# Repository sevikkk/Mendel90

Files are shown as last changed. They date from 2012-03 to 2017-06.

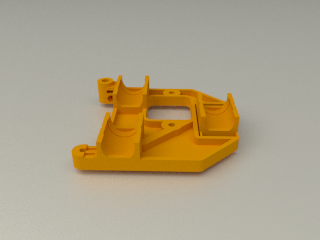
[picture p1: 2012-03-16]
sturdy/render/x_carriage.png

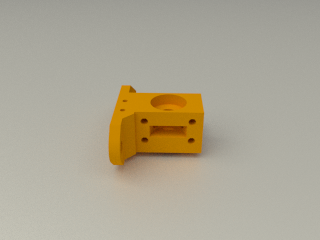
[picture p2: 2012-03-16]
sturdy/render/wades_block.png

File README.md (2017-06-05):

Standard variants
-----------------
[dibond](https://github.com/nophead/Mendel90/tree/master/dibond) is the version that was sold as a kit with 3mm sheets, 8mm rods and uses nuts and machine screws through the frame.

[sturdy](https://github.com/nophead/Mendel90/tree/master/sturdy) is 12mm MDF sheets, 10mm rods and uses wood screws into pilot holes in the frame. It can be built without CNC.

[mendel](https://github.com/nophead/Mendel90/tree/master/mendel) is 6mm acrylic sheets with a 10mm acrylic base, 8mm rods and uses machine screws into tapped holes in the frame.

[huxley](https://github.com/nophead/Mendel90/tree/master/huxley) is a scaled down version of dibond using 6mm rods and NEMA14 motors.

The dibond, sturdy and mendel versions can be modified to accept the E3D v6 hot end. The files that change are [dibond_E3D](https://github.com/nophead/Mendel90/tree/master/dibond_E3D)
and [sturdy_E3D](https://github.com/nophead/Mendel90/tree/master/sturdy_E3D).

Limitations
-----------
The dibond and sturdy versions are well tested and popular. The acrylic version, called mendel, hasn't been built for a long time and is not recommened.
The Huxley version hasn't been tested in its final form although one prototype has been made of an earlier version and a few snags fixed since.

Use
---
Add the directory of the OpenScad executable to your search path. OpenSCAD-2015.05 or later is required.
To get PDF versions of the sheet drawings add InkScape to your search path.

To make all the files for a machine run
```python
make_machine.py machine_name
```

To make just the bom, sheets or stls run bom.py, sheets.py or stls.py machine\_name.

machine\_name can be dibond, mendel, sturdy or huxley. To make your own variant copy scad\conf\mendel\_config.scad or scad\conf\sturdy\_config.scad to yourname\_config.scad.  Then run `make_machine.py yourname`.

To view the model of the whole machine, open scad\main.scad. It will take several minutes to render (about about 5 minutes on my computer) but after that you can pan and zoom it at reasonable speed and changes takes less time to render.  (Note: main.scad will only render correctly if conf\machine.scad exists, which is created by the make_machine.py script.)

To view a sub-assembly, open the individual scad files. Set the exploded flag in config.scad to make exploded views.

To get blender renders of all the parts put blender in your search path and run `render.py machine_name`.

Credits
-------
Fan model based on [this model](http://www.thingiverse.com/thing:8063) by MiseryBot, CC license.

[Sanguinololu model](http://www.thingiverse.com/thing:18606) by ax\_the\_b, CC license.

Spring taken from openscad example 20

x-end.scad and wade.scad use some elements of the Prusa ones by Josef Prusa, GPL license.

z_couplings originally based on [this model](http://www.thingiverse.com/thing:7153) by Griffin_Nicoll, GPL license.

Bearing holders originally based on [this model](http://www.thingiverse.com/thing:7755) by Jolijar, CC license.

InkCL.py based on [this code](http://kaioa.com/node/42)

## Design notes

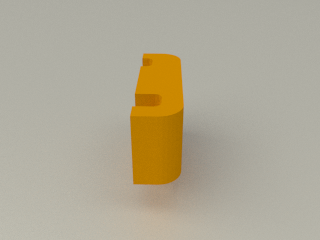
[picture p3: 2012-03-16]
sturdy/render/cable_clip_AB.png

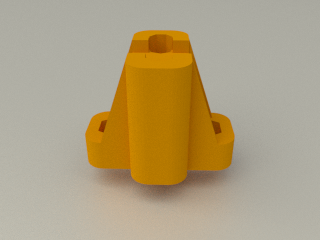
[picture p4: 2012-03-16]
sturdy/render/y_belt_anchor.png

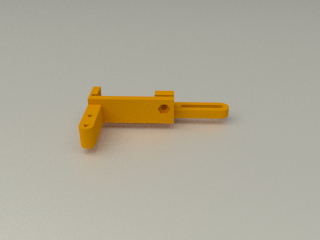
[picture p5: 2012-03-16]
sturdy/render/z_limit_switch_bracket.png

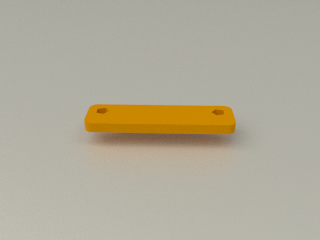
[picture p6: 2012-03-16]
sturdy/render/d_shell_lid.png

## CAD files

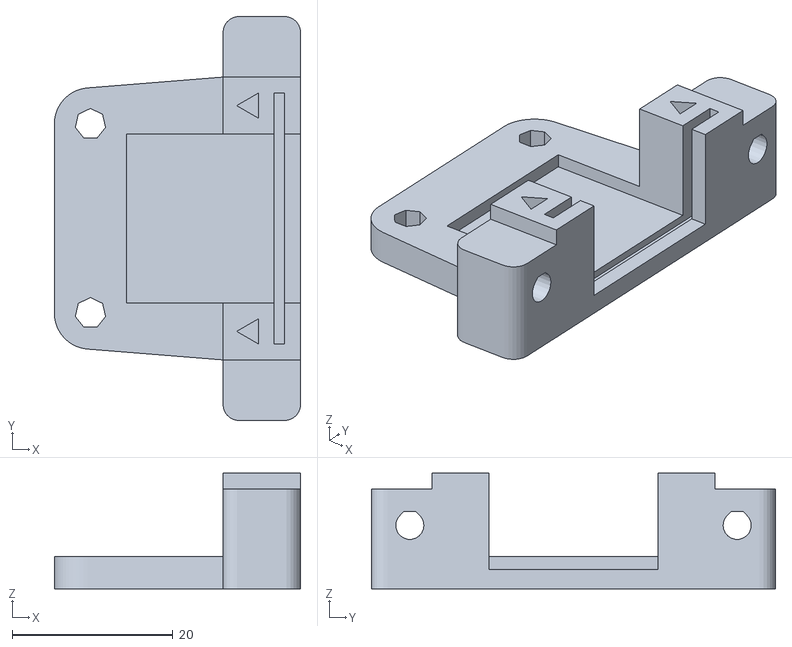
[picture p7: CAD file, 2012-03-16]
mendel/stls/d_shell.stl
30.7 x 50.3 x 14.4

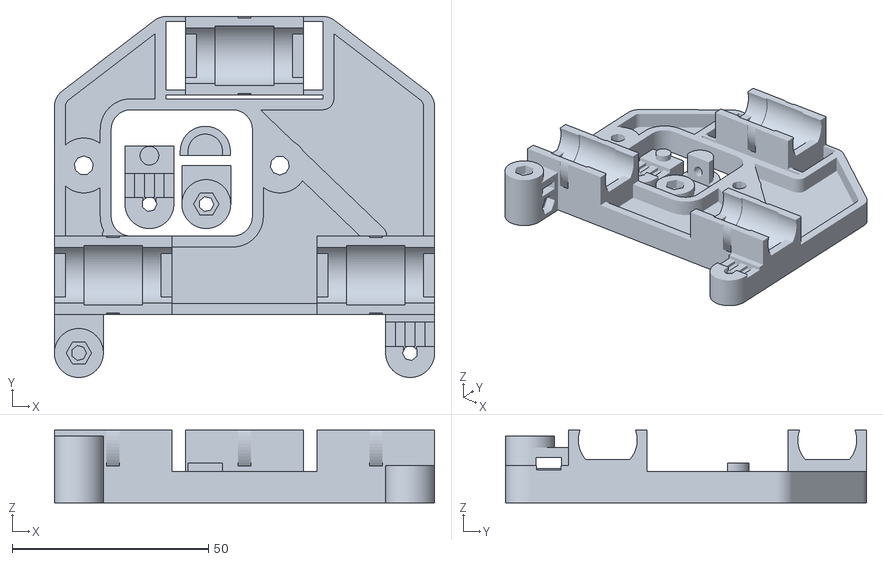
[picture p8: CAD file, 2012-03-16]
mendel/stls/printed/x_carriage_parts.stl
97.0 x 92.1 x 18.5

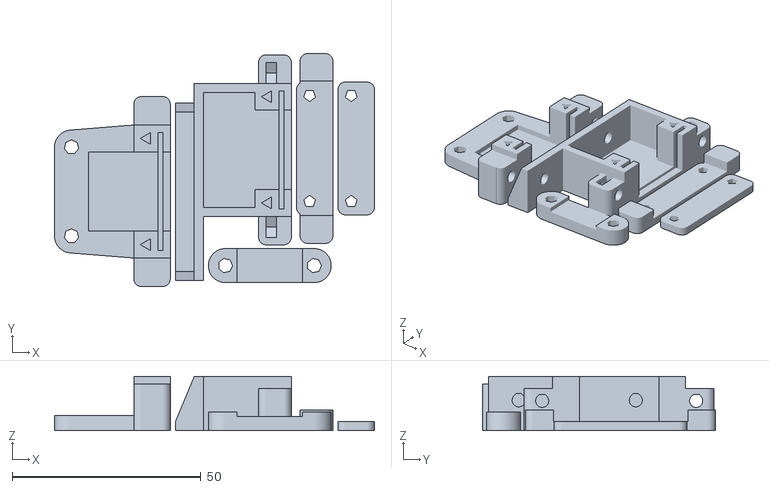
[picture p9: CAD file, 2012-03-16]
sturdy/stls/printed/d_motor_brackets.stl
84.7 x 61.7 x 14.4

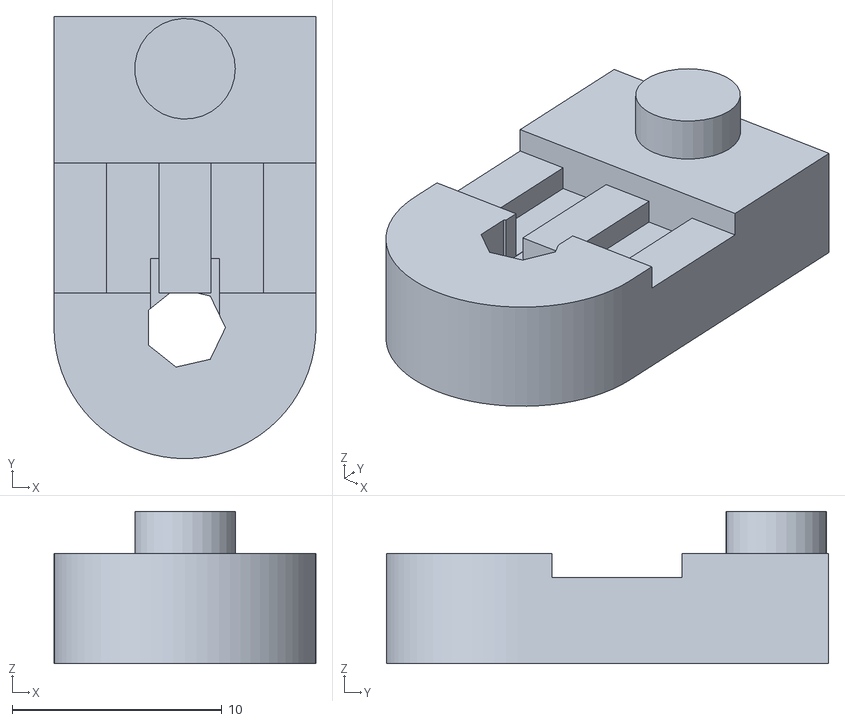
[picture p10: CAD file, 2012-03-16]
sturdy/stls/x_belt_grip.stl
12.5 x 21.1 x 7.26

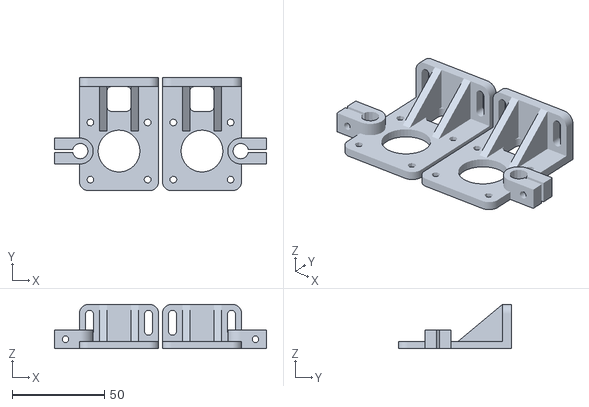
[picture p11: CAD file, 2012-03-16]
mendel/stls/printed/z_motor_brackets.stl
115.0 x 61.5 x 24.0

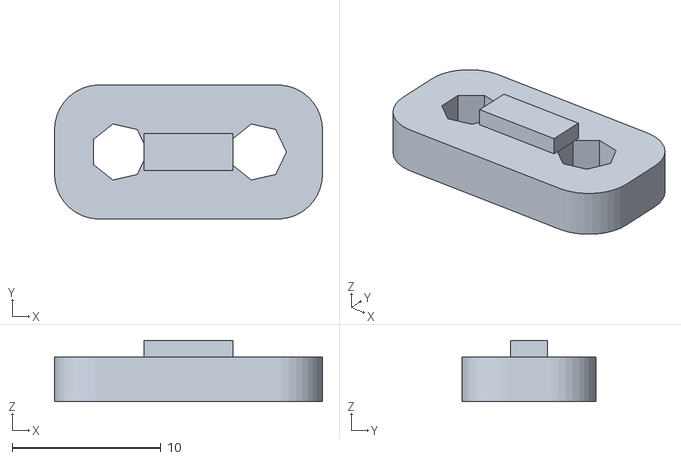
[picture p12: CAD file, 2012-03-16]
mendel/stls/y_belt_clip_toothed.stl
18.0 x 9.00 x 4.12

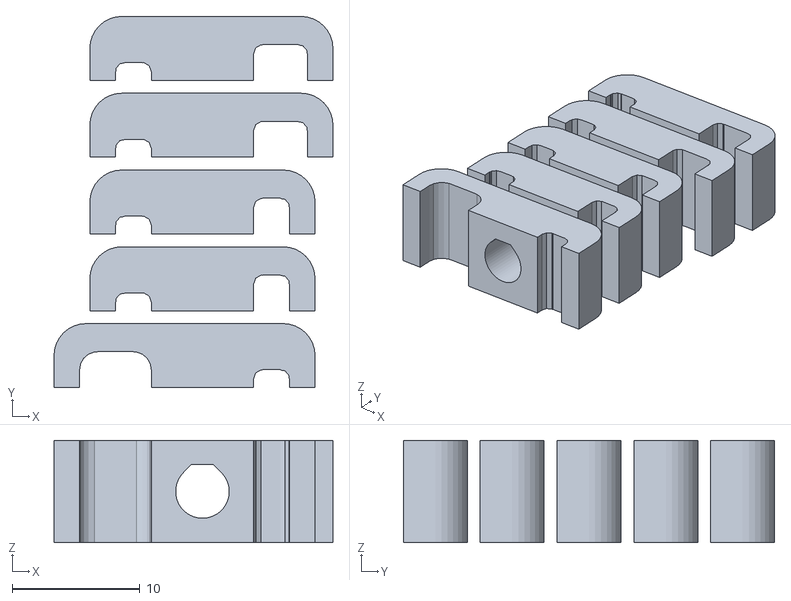
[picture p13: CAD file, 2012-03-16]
sturdy/stls/printed/cable_clips.stl
21.8 x 29.0 x 8.00

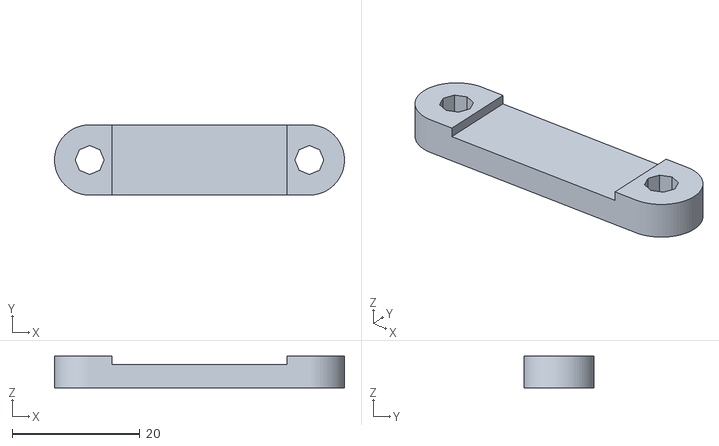
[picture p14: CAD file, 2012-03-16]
sturdy/stls/ribbon_clamp_20_40.stl
45.4 x 11.0 x 5.00

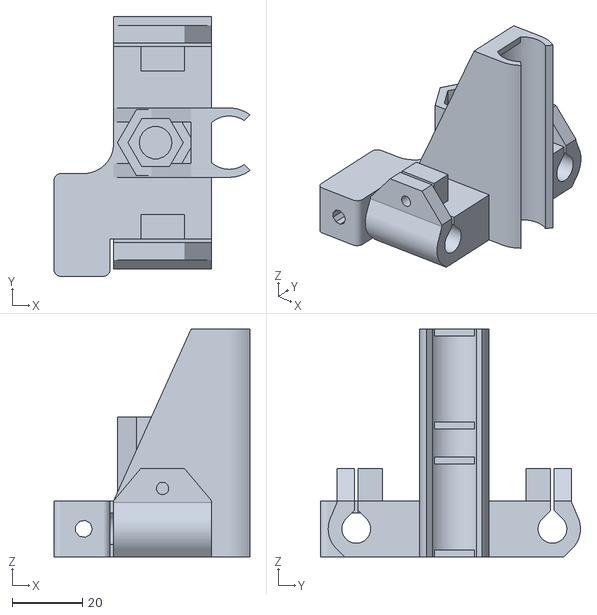
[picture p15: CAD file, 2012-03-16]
mendel/stls/printed/x_idler_bracket.stl
55.9 x 74.2 x 65.0

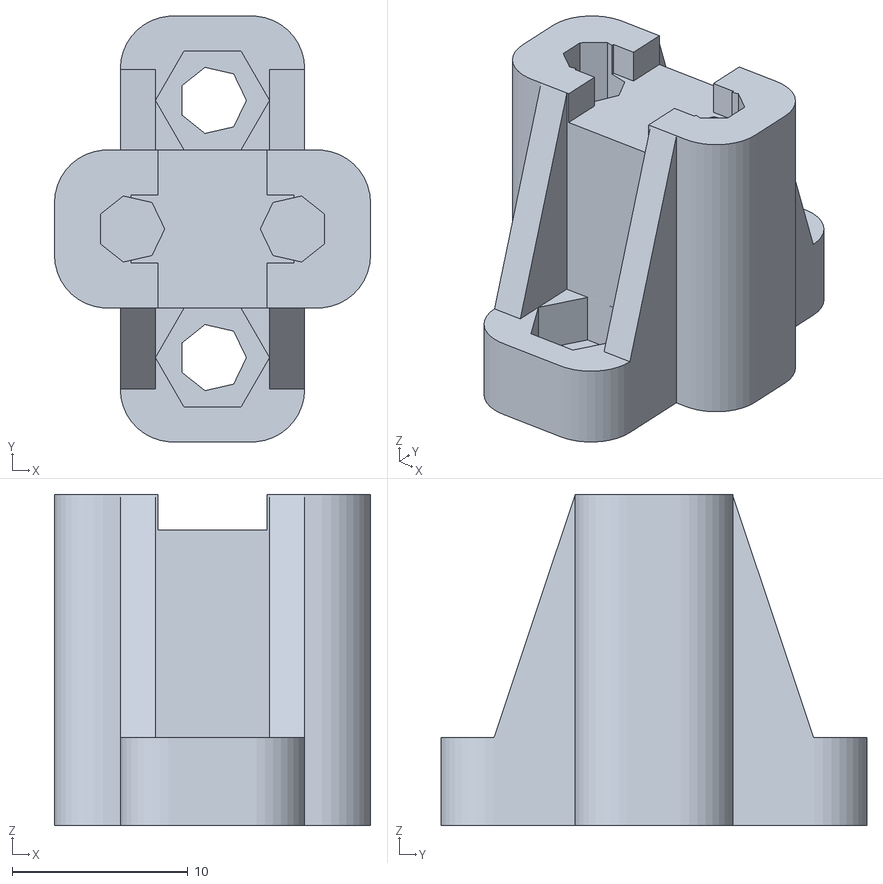
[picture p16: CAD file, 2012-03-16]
mendel/stls/y_belt_anchor.stl
18.0 x 24.3 x 18.9

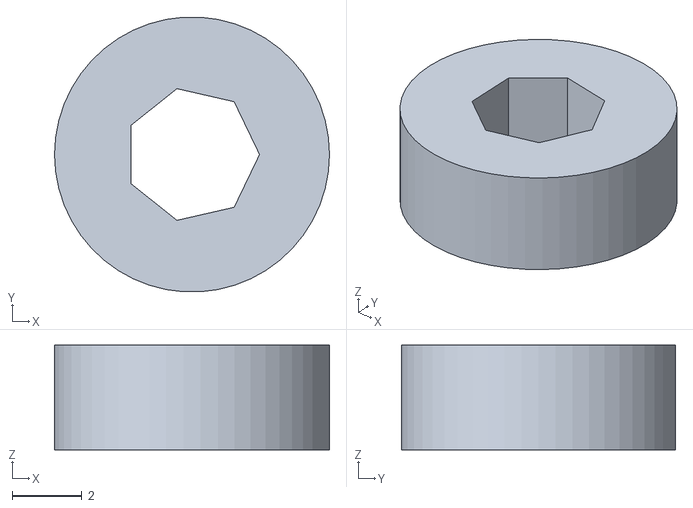
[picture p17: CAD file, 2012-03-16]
sturdy/stls/printed/pcb_spacer.stl
7.86 x 7.85 x 3.00

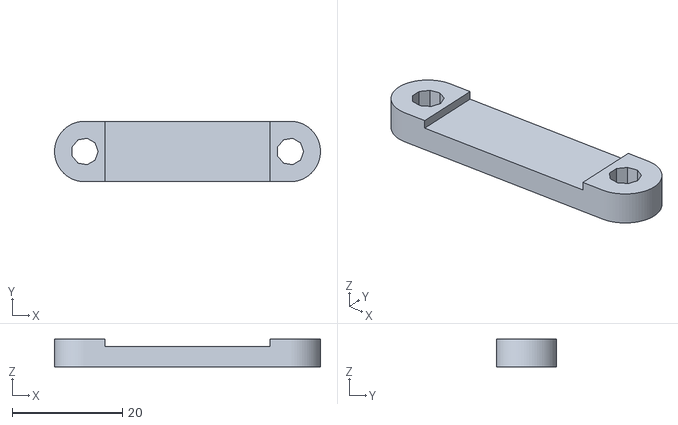
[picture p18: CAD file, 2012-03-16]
sturdy/stls/ribbon_clamp_22_44.stl
48.3 x 11.0 x 5.00

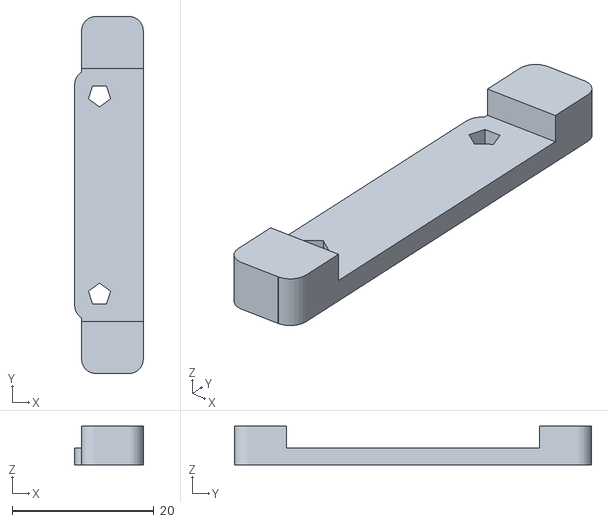
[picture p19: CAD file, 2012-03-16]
mendel/stls/d_motor_bracket_lid.stl
9.67 x 50.3 x 5.45

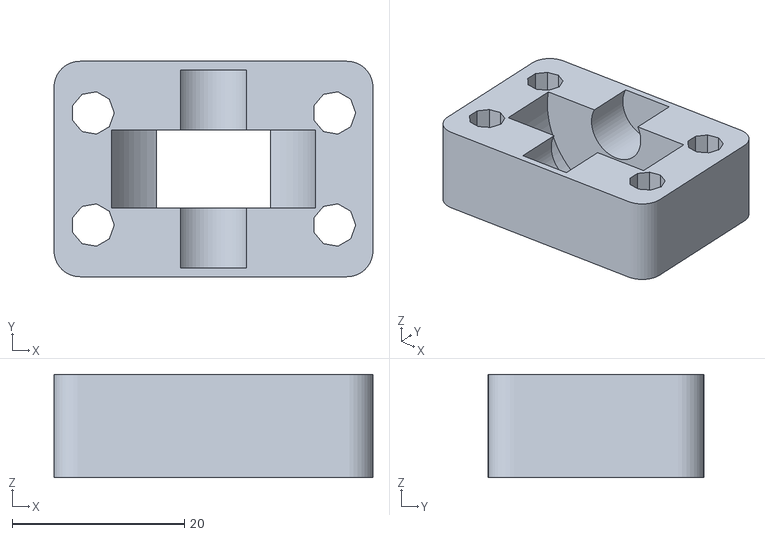
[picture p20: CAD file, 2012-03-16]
mendel/stls/printed/wades_idler_block.stl
37.0 x 25.0 x 12.0

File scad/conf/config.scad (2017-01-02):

//
// Mendel90
//
// GNU GPL v2
// nop.head@gmail.com
// hydraraptor.blogspot.com
//
// Configuration file
//
bom = $bom == undef ? 0: $bom;                 // 0 no bom, 1 assemblies and stls, 2 vitamins as well
exploded = $exploded == undef ? 0 : $exploded; // 1 for exploded view

show_jigs = true;               // show printed jigs required to build the machine
show_support = true;            // show support structures, must be set when generating STLs
show_rays = false;              // show light and camera rays to check orientation is correct

// Real-world colors for various parts & vitamins
use_realistic_colors = false;    // true for "real" colors, false for "distinct" colors (useful during design and for build instructions)
printed_plastic_color = "blue";
cable_strip_real_color = "fuchsia";
belt_real_color = "yellow";
bulldog_real_color ="black";

eta = 0.01;                     // small fudge factor to stop CSG barfing on coincident faces.
$fa = 5;
$fs = 0.5;

function sqr(x) = x * x;            // shortcut

module rotate(a)
{
 cx = cos(a[0]);
 cy = cos(a[1]);
 cz = cos(a[2]);
 sx = sin(a[0]);
 sy = sin(a[1]);
 sz = sin(a[2]);
 multmatrix([
  [ cy * cz, cz * sx * sy - cx * sz, cx * cz * sy + sx * sz, 0],
  [ cy * sz, cx * cz + sx * sy * sz,-cz * sx + cx * sy * sz, 0],
  [-sy,      cy * sx,                cx * cy,                0],
  [ 0,       0,                      0,                      1]
 ]) children();
}

cnc_tool_dia = 2.4;
layer_height = 0.4;
filament_width = layer_height * 1.5;
min_wall = 2 * filament_width + eta;
part_base_thickness = 5;;           // The thickness of things screwed to the frame

pcb_thickness = 1.6;
feed_tube_rad = 5 / 2;              // Filament feed tube
feed_tube_tape_rad = 6.2 / 2;
feed_tube_tape = 12;
function nozzle_length(hot_end) = max(54, hot_end_length(hot_end));    // how far nozzle extends below top of carriage

include <colors.scad>
include <utils.scad>
include <vitamins.scad>

endstop_wires    = [2, 1.4, "A"];   // 7 strands of 0.2
motor_wires      = [4, 1.4, "B"];
bed_wires        = [2, 2.8, "C"];   // 13A mains cable
fan_motor_wires  = [6, 1.4, "D"];   // fan and motor wires along top of gantry
two_motor_wires  = [8, 1.4,,"E"];   // Y and Z motors
thermistor_wires = endstop_wires;

endstop_wires_hole_radius = wire_hole_radius(endstop_wires);
motor_wires_hole_radius = wire_hole_radius(motor_wires);
two_motor_wires_hole_radius = wire_hole_radius(two_motor_wires);
fan_motor_wires_hole_radius = wire_hole_radius(fan_motor_wires);
bed_wires_hole_radius = wire_hole_radius(bed_wires);
thermistor_wires_hole_radius = wire_hole_radius(thermistor_wires);

cnc_sheets = false;                 // If sheets are cut by CNC we can use slots, etc instead of just round holes
base_nuts = false;                  // Need something under the base if using nuts
pulley_type = T5x8_plastic_pulley;
clip_handles = true;
include_fan = false;
squeeze = false;                    // Bodge to make Huxley as small as possible without affecting dibond kits
part_fan = fan60x15;
extruder = Wades;                   // Default extruder
raspberry_pi = false;               // Raspberry pi mounted on PSU
raspberry_pi_camera = false;        // RPI camera on bar across the back
light_strip = false;
vero_bed = false;                   // Bed made from vero board rather than custom PCB.
include <machine.scad>              // this file is generated from the command line parameter to include one of the machine configs

screw_clearance_radius = screw_clearance_radius(cap_screw);
nut = screw_nut(cap_screw);
nut_radius = nut_radius(nut);
nut_trap_depth = nut_trap_depth(nut);
washer = screw_washer(cap_screw);

bearing_clamp_tab = cnc_sheets ? (nut_radius(nut) + 3 * filament_width) * 2 : washer_diameter(washer) + 2;   // how much the lugs stick out and their width
bearing_clamp_tab_height = 4;           // thickness of the lugs

hole_edge_clearance = 5;                // how close a hole can be to the edge of a sheet
base_clearance = cnc_sheets ? 1 : 2;    // how close we get to the edge of the base
axis_end_clearance = cnc_sheets ? 1 : 2;// how close we get to the end of an axis
limit_switch_offset = 1;                // the over travel to reach the limit switch
X_carriage_clearance = 2;               // how close the X carriage is to the XZ plane
                                        // how close the Y carriage is to the window in the XZ plane
Y_carriage_clearance = 2 + (clip_handles ? (bulldog_handle_length(small_bulldog) - (Y_carriage_width - bed_width) / 2) : 0);
Y_carriage_rad = 3;                     // corner radius
Z_clearance = 10;                       // How close the top of the object gets to the gantry
belt_clearance = 0.2;                   // clearance of belt clamp slots

X_bar_dia = bearing_rod_dia(X_bearings);      // rod sizes to match the bearings
Y_bar_dia = bearing_rod_dia(Y_bearings);
Z_bar_dia = bearing_rod_dia(Z_bearings);

Y_idler_bearing = BB624;
X_idler_bearing = BB624;

extruder_ways = 4 + 6 + 2 + 1 + 1;      // motor + heater(x3) + thermistor + probe + fan = 14
x_end_ways = extruder_ways + 4 + 2;     // motor plus limit switch = 20
bed_ways = 24 + 2;                      // twelve each way for the current plus a thermistor

module wire_hole_or_slot(r) {
    if(cnc_sheets)
        rotate([0, 0, 90])
            slot(r = r, h = 100, l = 2 * r);
    else
        translate([0, r + hole_edge_clearance, 0])
            wire_hole(r);
}

function z_bar_offset() = round(NEMA_width(Z_motor)) / 2  + ((Z_bar_dia > 10) ? ((Z_bar_dia - 10) / 2) : 0);
echo("Z: ", z_bar_offset());

base_screw = sheet_is_soft(base) ? frame_soft_screw : (base_nuts ? frame_thin_screw : frame_thick_screw);
base_nut = base_nuts ? screw_nut(base_screw) : false;
base_nut_traps = base_nuts && cnc_sheets;
base_washer = screw_washer(base_screw);
base_screw_length = base_nuts ? screw_longer_than(
                                    sheet_thickness(base)
                                    + part_base_thickness +
                                    (cnc_sheets ? 1 : 2) * washer_thickness(base_washer)
                                    + nut_thickness(base_nut, true)
                                  )
                              : screw_shorter_than(
                                    sheet_thickness(base)
                                    + part_base_thickness
                                    + 2 * washer_thickness(base_washer)
                                 );


frame_screw = sheet_is_soft(frame) ? frame_soft_screw : (frame_nuts ? frame_thin_screw : frame_thick_screw);
frame_nut = frame_nuts ? screw_nut(frame_screw) : false;
frame_nut_traps = frame_nuts && cnc_sheets;
frame_washer = screw_washer(frame_screw);
frame_screw_length = frame_nuts ? screw_longer_than(
                                      sheet_thickness(frame)
                                      + part_base_thickness +
                                      (cnc_sheets ? 1 : 2) * washer_thickness(frame_washer)
                                      + nut_thickness(frame_nut, true)
                                  )

                                : screw_shorter_than(
                                      sheet_thickness(frame)
                                      + part_base_thickness
                                      + 2 * washer_thickness(frame_washer)
                                  );

echo("base screw length", base_screw_length);
echo("frame screw length",frame_screw_length);



module frame_screw(thickness) {
    if(frame_nuts && cnc_sheets) {
        nut(frame_nut, true);
        translate([0, 0, -sheet_thickness(frame) - thickness])
            rotate([180, 0, 0])
                screw_and_washer(frame_screw, frame_screw_length);
    }
    else {
        screw_and_washer(frame_screw, frame_screw_length, !frame_nuts);
        if(frame_nuts)
            translate([0, 0, -sheet_thickness(frame) - thickness])
                rotate([180, 0, 0])
                    nut_and_washer(frame_nut, true);
    }
}

module frame_screw_hole() {
    cylinder(r = frame_nuts ? screw_clearance_radius(frame_screw) : screw_pilot_hole(frame_screw), h = 100, center = true);
}



module base_screw(thickness) {
    if(base_nuts && cnc_sheets) {
        nut(base_nut, true);
        translate([0, 0, -sheet_thickness(base) - thickness])
            rotate([180, 0, 0])
                screw_and_washer(base_screw, base_screw_length);
    }
    else {
        screw_and_washer(base_screw, base_screw_length, !base_nuts);
        if(base_nuts)
            translate([0, 0, -sheet_thickness(base) - thickness])
                rotate([180, 0, 0])
                    nut_and_washer(base_nut, true);
    }
}

module base_screw_hole() {
    cylinder(r = base_nuts ? screw_clearance_radius(base_screw) : screw_pilot_hole(base_screw), h = 100, center = true);
}
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

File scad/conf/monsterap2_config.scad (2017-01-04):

//
// Mendel90
//
// GNU GPL v2
// nop.head@gmail.com
// hydraraptor.blogspot.com
//
// Configuration file
//
echo("Sturdy:");

Z_bearings = LM16UU;
Y_bearings = LM16UU;
X_bearings = LM16UU;

X_motor = NEMA17;
Y_motor = NEMA17;
Z_motor = NEMA17;

hot_end = JHeadMk5;

X_travel = 300;
Y_travel = 246;
Z_travel = 352;

bed_depth = 250;
bed_width = 260;
bed_pillars = M3x20_pillar;
bed_glass = glass2;
bed_thickness = pcb_thickness + sheet_thickness(bed_glass);    // PCB heater plus glass sheet
bed_holes = [255, 245];

base = MDF12;
base_corners = 0;

frame = MDF12;
frame_corners = 0;
frame_nuts = false;

case_fan = fan80x38;
psu = ALPINE500;
//psu = KY240W;
controller = Melzi;
//controller = Sanguinololu;
spool = spool_300x85;
bottom_limit_switch = false;
top_limit_switch = true;

single_piece_frame = true;
stays_from_window = false;

Y_carriage = DiBond;

pulley_type = GT2x20_metal_pulley;
X_belt = GT2x6;
Y_belt = GT2x6;

motor_shaft = 5;
Z_screw_dia = 6;            // Studding for Z axis

Y_carriage_depth = bed_holes[1] + 8;
Y_carriage_width = bed_holes[0] + 8;

Z_nut_radius = M6_nut_radius;
Z_nut_depth = M6_nut_depth;
Z_nut = M6_nut;

//
// Default screw use where size doesn't matter
//
cap_screw = M4_cap_screw;
hex_screw = M4_hex_screw;
//
// Screw for the frame and base
//
frame_soft_screw = No6_screw;               // Used when sheet material is soft, e.g. wood
frame_thin_screw = M4_cap_screw;            // Used with nuts when sheets are thin
frame_thick_screw = M4_pan_screw;           // Used with tapped holes when sheets are thick and hard, e.g. plastic or metal
//
// Feature sizes
//
default_wall = 4;
thick_wall = 4;

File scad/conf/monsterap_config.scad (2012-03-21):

//
// Mendel90
//
// GNU GPL v2
// seva@sevik.org
//
// Configuration file for Monsterap
//
// https://picasaweb.google.com/114257244810512271993/Monsterap
//
echo("Monsterap:");
// Local vitamins

M12_nut_depth = 9.5;
M12_nut_radius = 11;
M12_washer =      [12, 22, 1.5, false];
M12_nut = [12, 21,  9.5, 8, M12_washer, M12_nut_depth];
LM16UU = [30, 24, 16];
T5x8 =  [5, 8,  2.25];
MDF18    = [ "MD", "MDF sheet",    18, [0.4, 0.4, 0.2, 1    ], true];
NEMA17M  = [42.3, 39.5,   53.6/2, 25,     11,     2,     5,     24,     31 ];


Z_bearings = LM16UU;
Y_bearings = LM16UU;
X_bearings = LM16UU;

X_motor = NEMA17M;
Y_motor = NEMA17M;
Z_motor = NEMA17M;

X_travel = 303;
Y_travel = 250;
Z_travel = 300 + (500-426.5);

bed_depth = 310;
bed_width = 310;
bed_pillars = M3x20_pillar;
bed_glass = glass2;
bed_thickness = 1.6 + sheet_thickness(bed_glass);    // PCB heater plus glass sheet
bed_holes = 305;

base = MDF18;
base_corners = 0;

frame = MDF12;
frame_corners = 0;
frame_nuts = false;

case_fan = fan80x38;
psu = KY240W;

single_piece_frame = true;
stays_from_window = false;

Y_carriage = DiBond;

extruder_width = 30;        // actually 28 but offset
nozzle_x_offset = 16;       // offset from centre of the extruder
nozzle_length = 50;         // from base of extruder to nozzle tip

X_belt = T5x8;
Y_belt = T5x8;

motor_shaft = 5;
Z_screw_dia = 8;            // Studding for Z axis

Y_carriage_depth = bed_depth + 10;
Y_carriage_width = bed_width + 10;

Z_nut_radius = M8_nut_radius;
Z_nut_depth = M8_nut_depth;
Z_nut = M8_nut;

//
// Default screw use where size doesn't matter
//
cap_screw = M4_cap_screw;
hex_screw = M4_hex_screw;
//
// Screw for the frame and base
//
frame_soft_screw = No6_screw;               // Used when sheet material is soft, e.g. wood
frame_thin_screw = M4_cap_screw;            // Used with nuts when sheets are thin
frame_thick_screw = M4_pan_screw;           // Used with tapped holes when sheets are thick and hard, e.g. plastic or metal
//
// Feature sizes
//
default_wall = 4;
thick_wall = 4;

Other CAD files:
sturdy/stls/printed/cal.stl
sturdy/stls/y_bar_clamp.stl
mendel/stls/printed/y_idler_bracket.stl
mendel/stls/ribbon_clamp_20_44.stl
scad/z-motor-bracket.scad
mendel/stls/cable_clip_CA.stl
mendel/stls/d_motor_bracket.stl
mendel/stls/d_shell_lid.stl
mendel/stls/printed/bar_clamps.stl
mendel/stls/printed/cable_clips.stl
mendel/stls/printed/cal.stl
mendel/stls/printed/d_motor_brackets.stl
mendel/stls/printed/fan_guard.stl
mendel/stls/printed/fixing_block.stl
mendel/stls/printed/pcb_spacer.stl
mendel/stls/printed/pulley.stl
mendel/stls/printed/ribbon_clamps.stl
mendel/stls/printed/wades_big_gear.stl
mendel/stls/printed/wades_block.stl
mendel/stls/printed/wades_gear_spacer.stl
mendel/stls/printed/wades_small_gear.stl
mendel/stls/printed/x_motor_bracket.stl
mendel/stls/printed/y_bearing_mounts.stl
mendel/stls/printed/y_belt_anchors.stl
mendel/stls/printed/y_motor_bracket.stl
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

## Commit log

2012-03-15 config for my machine
    new part sizes for vitamins
    [belts.scad, config.scad, linear-bearings.scad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]
2012-03-15 config changes like in upstream
    [monsterap_config.scad, sheet.scad]
2012-03-15 z bar to 500mm
    total depth limited to 600mm
    [monsterap_config.scad]
2012-03-16 moved local vitamins to config file
    revert scad/vitamins to upstream version
    [belts.scad, config.scad, linear-bearings.scad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]
2012-03-16 forgotten vitamins
    [monsterap_config.scad]
2012-03-16 with bigger rods internal hole cuts into rod clamp
    This is temporary solution, right one must use minimum of current value
    and value constrained by rod bottom
    [bar-clamp.scad]
2012-03-16 modify y-bar bearings inset to shorten y-bar to 500 mm
    [main.scad]
2012-03-16 master closely tracks upstream
    all changes relevant to monsterap moved to monsterap branch
    [monsterap_config.scad]
2012-03-16 config file brought back
    [monsterap_config.scad]
2012-03-18 smaller panels for my current printer
    [bar-clamp.scad]
2012-03-18 increase clamps depth so inner nut hole does not cut into wall
    [config.scad]
2012-03-19 dual endstop for Y-axis
    small panel with 2 mounts only
    [y-bearing-mount.scad]
2012-03-19 8mm z-screw
    [monsterap_config.scad]
2012-03-20 shorter stepper motor
    cut x motor bracket to fit current printer size
    removed cable mounts
    added mount holes for back side of motor
    z nut rotated 30 degrees so it cuts in bearing mounts less
    [monsterap_config.scad, x-end.scad]
2012-03-21 panel with all couplers
    [z-coupling.scad]
2012-03-21 copyright and picassa link :)
    [monsterap_config.scad]
2012-04-05 changes for smaller buildarea of current printer
    [bar-clamp.scad, wade.scad, x-carriage.scad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]
2012-04-06 mounting brackets for mk7 extruder
    [mk7_bracket.scad]
2012-04-08 ribbon clamp for two cables
    [ribbon_clamp.scad]
2012-04-14 pcb mounts
    [fixing-block.scad]
2017-01-01 current state for old build
    [wade.scad, x-carriage.scad, x-end.scad]
2017-01-02 rotate z bar clamps, so they are symmetric
    [bar-clamp.scad, main.scad, z-motor-bracket.scad]
2017-01-02 monsterap2 initial config, more space for z-coupler
    [config.scad, linear-bearings.scad, monsterap2_config.scad]
2017-01-02 build monsterap2 by default
    [machine.scad]
2017-01-02 some hackish adjustments
    [bar-clamp.scad, main.scad, nuts.scad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]
2017-01-04 adjustments to fit rods length
    [main.scad, monsterap2_config.scad, x-carriage_assembly.scad]
2017-01-04 second x-carriage
    [positions.scad, x-end.scad]
2017-12-10 Changes to cope with SolidPython parser deficiences
    [x-end.scad]
2017-12-10 Simple SolidPython Connectors implementation
